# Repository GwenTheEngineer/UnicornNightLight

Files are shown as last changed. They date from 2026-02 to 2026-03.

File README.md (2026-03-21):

# Unicorn Night Light

This is the first time I've documented and open-sourced a weekend project!

If this project is helpful, you can support future side quests ☕
https://buymeacoffee.com/GwenTheEngineer

[YouTube playlist](https://www.youtube.com/playlist?list=PLPH9-bBXNwrTy-LLMLCjv-cOZETsQUVa1) for this project.

## Idea
This project brings to life the following vision for a table-top night light.

* Unicorn shaped shell
* Star shaped holes (through which the light will project)
* Moves up and down .... but *not* in circles (to avoid the user getting dizzy)
* Preferably rainbow colored

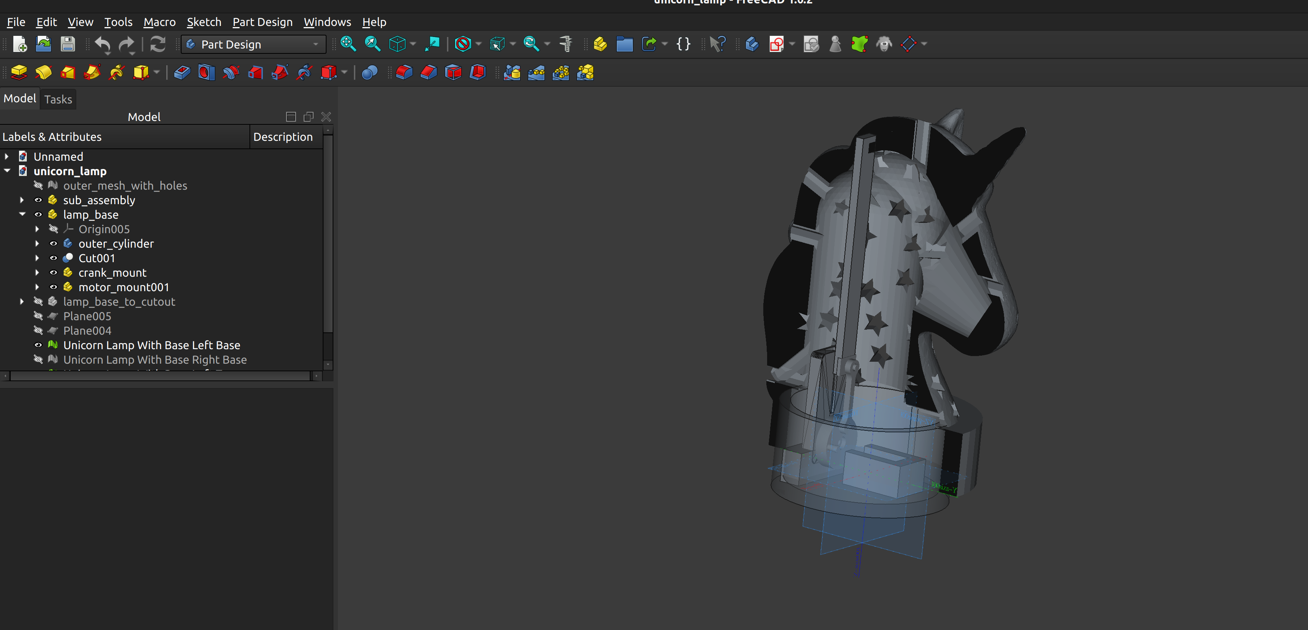
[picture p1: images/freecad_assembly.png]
Unicorn Nightlght Assembly


## Conceptual Design

A back of the envelope sketch of the vision! Doesn't need to be perfect, just needs to communicate what we want to accomplish. 

## Research

### Printable Parts

First, I needed a mechanism that could convert angular movement to linear movement...but I didn't know the right word for it. So I googled. Turns out, the word is "crank". Then, because my CAD skills are pretty elementary, I searched by go-to resource (printables.com) for a model that would work as a starting point -- with some resizing and adjusting to accommodate the motor shaft.

### Electrical and Mechanical

My hardware-adjacent and hobby background helped here. I hopped on amazon to find a low speed motor, appropriate transformers and adapters, and some LEDs and heat sinks. The complete BOM is listed below (NOTE! s.t. change; will remove this note when the project works).

Key considerations if you're shopping for your own parts:
* Motor size and speed -- I wanted something small (to fit inside) and low speed, but high enough torque to deal with the weight of the head and friction of the crank.
* Power supply -- wall sockets are AC; almost all hobby parts need DC
* Match voltages -- motor calls for 3.3-5V; you may need to step down your voltage after you transform AC-->DC
* Heat -- heat sinks help keep the temperature down.
* Materials! (see error log) Turns out after a few minutes, the PLA printing material deforms enough so the the outer shell stops going up and down (which is the whole point). Swapped to RC car pinion gears instead of directly driving the crank from the motor. 

## Detailed Mechanical Design

### CAD

I'm an engineer, but not *this* kind of engineer (professionally, at least). I did play with meshes in grad school, and CAD for mechanical design as an undergrad, but I was rusty when I started this project.

### Tl;dr

* I used FreeCAD (https://www.freecad.org/), Blender  (https://www.blender.org/), and Tinkercad (https://www.tinkercad.com/)
* Blender for mesh coarsening (in order to import the unicorn head mesh into FreeCAD and Tinkercad)
* FreeCAD to create the primitives to hollow out the head
* Tinkercad for booleam operations (i.e., actually subtracting the hole from the shell; adding the star holes)
* FreeCAD to ensure mechanical fit of the crank parts and motor mount and extending the slider / attaching it to the outer unicorn head shell
* Tinkercad for final adjustments (adding a collar, subtracting the base, making the hole to attach the slider column to the unicorn shell)
* FreeCAD for tweaking hole sizes to fit the motor and adding a through hole for the power cable to the base.
* FreeCAD to extend the slider mount (by slicing and tiling the original) and add a second bearing to the extended slider column
* ~~Blender to bisect the unicorn head in order to fit it on my printer (a Prusa Mini) -- See notes; this was a fun exercise but did not turn out to be necessary~~

### Play by Play
#### Outer Shell
Like most projects, this turned out to be more complicated than I had originally envisioned. (Engineers are notoriously bad at estimating).

Professional CAD tools are expensive. My favorite tool for small projects because it's very easy to use is tinkercad (online-only tool from the makers of AutoCad), free for individual and educational purposes.

For this project, that wouldn't work because the unicorn mesh was too big. After some research, I selected FreeCAD. Don't forget to leave a donation!

The big mesh was still causing problems, and free cads discretization didn't "just work". It's been a hot second, but I have used Blender for generating graphics for academic projects in the past. So I installed Blender, imported the mesh, used Blender's decimation tools, then went back to FreeCAD.  

After refining the mesh, I imported it back into FreeCad, then used primitives (cylinders, spheres, cones) to hollow out the unicorn head.

Next pain point was converting the unicorn shell to a solid in order to subtract the hole. FreeCAD recommends a max of 20k triangles; it was still too big (I tried to wait to let the CPU do it's thing, but it was hung)

But! Now I could import both parts into tinkercad and cut the hole out that way! So I decided to make the full shell in tinkercad, and return to FreeCAD (which I do want to learn) for the moving parts.

Back to FreeCAD to adapt the crank parts!

I imported the crank parts separately and "assembled" them for sense of scale. The general plan was to fit them in then scale the unicorn if necessary to make more room. I decided I would add mounts for the PCBs and LEDs later once all of the moving parts were put together. (Or, just wedge them in for now and come back to that in the next rev).

I needed one last import into free cad to cut the base out of the unicorn when all measurements were finalized. I scaled the unicorn up slightly from the original, and added a "cup" at the bottom to wedge PCBs and wires into.

One more round trop from FreeCAD to Tinkercad to get the hole at the bottom correctly sized; I had to add a collar (I just did this in Tinkercad) to maintain the wall thickness.

Finally! I split the unicorn by planes (in FreeCAD) and went to plate it ... forgetting that I needed to have the edges filled (with the cutout, it's just 2 nested meshes.) CAD programs generally aren't great at mesh editing. Back to Blender.

This article was useful: https://blender.stackexchange.com/questions/338870/bisect-separate-move. Don't forget to select "Fill" when you're bisecting. 

I rearranged the resulting objects into 2 collections, and duplicated the new faces in each collection, then, I went back to object mode and joined all objects, and then back to merge the meshes by distance (this removed a few hundred vertices each time).

#### Finalizing the Crank

~~First, I cleaned up the original mesh by removing the tab meant to demonstrate the part manually. I did this in Blender, but probably could have converted to a solid in FreeCAD and made the updates there, since it's a pretty simple mesh.~~  (see error log; this was actually not meant for fingers, it was a necessary part)

After the motors came in, I measured the shaft diameter at 3mm, with a flat face about 2mm wide. I then proceeded to accidentally use 3mm as the radius when updating the hole in the crank. F. This had to be redone. ~~On the bright side I only had to fix the hole in the crank, because the default size for the part attached to the base was just about right (I'll file it down after it prints if it's an issue).~~

#### Finalizing the Base
We need to punch a hole for the power cord to go through!

###### Rework #1 - crank orientation and hols sizing
I went ahead and made all of the holes bigger (1.8-2mm radius; see parts for details) for a better fit and reduce the amount of sanding I'd need to do for the mechanism to be smooth.

The slider mount needed to be flipped (:facepalm:). In the original orientation, the motor shaft would have interfered with the rod of the crank. To accomplish this in FreeCAD without changing the position of the column relative to the base, I placed the slider+column part directly over the crank to fit part, then rotated and adjusted the parts until the columns were overlapping the the crank was flipped 180 degrees relative to the motor mount.

I also extended the column by about 2cm to correct for the error of measuring the original height from slider's top position instead of the bottom. Oops.

###### Rework #2 - extend the slider mount; add 2nd bearing
I extended the slider mount and add a second bearing to limit the moment induced by the unicorn head on the slider. When mounted, it was pulling the crank off of the motor shaft.

###### Rework #3 - swap drive train; update parts accordingly
This was a pretty extensive rework. It involved updating the model to accommodate
(1) a gear attached to the end of the motor shaft, 
(2) a through-hole for the 2nd gear which will actually drive the crank, and
(3) adaptation of the crank parts to attach to a 3rd gear to drive the slider.

I did a save-as before starting this (new file is `unicorm_lamp_gears.FCStd`)

## Resources

### 3D Models

Crank Mechanism: https://www.printables.com/model/632627-crank-mechanism 

Unicorn Head: https://www.printables.com/model/1155402-unicorn-head

3D Printer: https://www.prusa3d.com/product/original-prusa-mini-semi-assembled-3d-printer-enclosure-bundle-5/

You don't actually need your own 3D printer; there is a growing number of public libraries, schools, and maker spaces where you can find them.

### BOM

These are affiliate links to fund a small percentage of reaching my Balmer peak (3-5% commission, depending on the part). Yay late stage capitalism. Let me know if you have a better resource and want to give Bezos less if your money.

As of this writing I have not tested any of these, so the list may change. I'll remove this comment when this is final.

#### Electrical Components
* Low speed (tiny) motors: https://amzn.to/4qAXlMr
* LEDs: https://amzn.to/469XHT5
* Heat sinks: https://amzn.to/3ZFIS6Y
* DC Low Voltage Speed Controller: https://amzn.to/4qSYteF
* Universal AC Adapter: https://amzn.to/4azepfL

#### Drive Train
* Steel RC Car Gears (38T and 42T used): https://amzn.to/47XY2c8
* Brass RC Car Gears (36T used): https://amzn.to/4bpC8AX
* 3mm Diameter Dowel: https://amzn.to/4bpC8AX 

(Same size in brass gears should be fine.)

#### Useful Tools
* Nail kit (useful for cleaning up support material from meshes): https://amzn.to/4s3IJGH
* Small electronics shopping cart (solder, wires, etc.). This is similar to what I've accumulated: https://amzn.to/4tOZ03W

## License

Unless otherwise noted, the documentation, images, and written content in this project are licensed under the Creative Commons Attribution-NonCommercial-ShareAlike 4.0 International License.

You are free to share and adapt this material for any non-commercial purpose, as long as you give appropriate credit.

## Disclaimer

This project is provided for educational and informational purposes only.

You assume all responsibility and risk for using the information, code, hardware designs, and instructions provided here. I make no guarantees regarding safety, reliability, or suitability for any purpose.

By attempting this project, you agree that I am not liable for any injury, damage, loss, or other issues that may occur as a result of building or using this project.

*Always follow proper safety practices when working with electronics, tools, and power sources.*

## Error Log (Learning!)

### Printing Orientation

Initially I thought of printing the unicorn on its side for 2 reasons (1) to fit on the build plate and (2) to minimize support material not directly on the build plate; i.e. to avoid digging support material out of the unicorns nose. The unicorn's horn did not stick to the plate -- it lifted. Also, the filament I'm using is rainbow -- so printing each side separately would cause a weird discontinuity in the rainbow. Since I had to bisect the head twice (X and Z planes) to fit anyways, I might as well try printing from the bottom up.... back to Blender. I also adjusted the settings (angle) when computing necessary support material.

*I reduced the angle to 45 degrees and swapped to organic support (which is often easier to remove).*

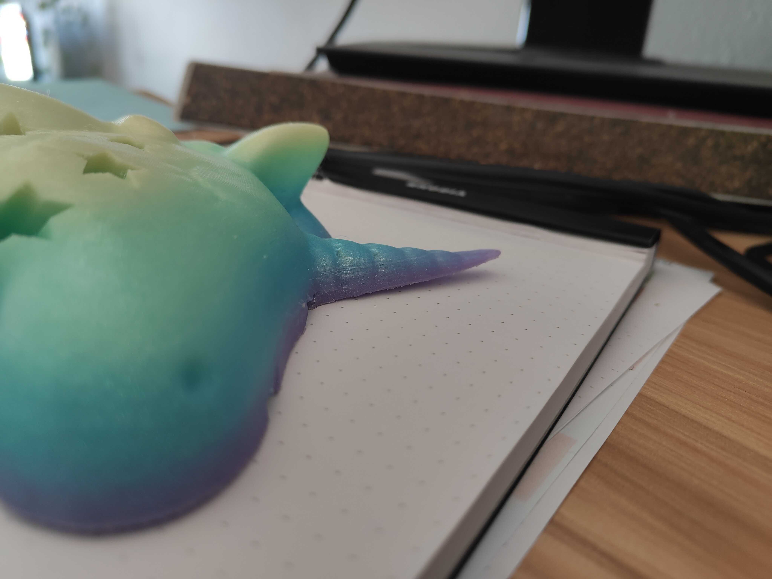
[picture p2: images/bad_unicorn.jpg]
Unicorn Nightlght Assembly


### Blender Hanging Splitting Loose Parts

The number of time Blender hung after bisect --> split faces by edges --> separate loose parts was frustrating. For some reason, it was trying to split ALL of the triangles into separate parts. This seemed to happen consistently when I bisected in the Z-plane (top from bottom) first.

In the end, I realized I could just print the whole unicorn, so went with this option (better for rainbow filament continuity).

The best work-around I found was duplicating the mesh and bisecting each instance; keeping the inner on one and outer on the other.

### Holes, Orientations, Mounts, and Tolerances

The motor shaft did not fit through the center holes on the crank. I went back to FreeCAD and made them 1.5mm wider. The hole on the crank mount was also too low by 1-2mm, so I moved that whole part up. I also upped the size of the holes in the crank's rod to reduce the amount of sanding I would need to do on the other crank parts to get a smooth motion.

In further facepalm-inducing mistakes, I computed the column height (the column connects the slider to the unicorn head) from the *top* position of the slider -- which meant it was several centimeters to short. This part also had to be redone.

Finally, the crank was actually backwards. The motor shaft and rod would interfere with each other. Oops.

Unicorn Nightlght Assembly

### Full Assembly Wobbles

Hindsight is always 20/20. With the base assembled, I was initially please with the fit of the motor shaft into the crank. The mechanism moved up and down about as smoothly as one would expect from PLA parts. HOWEVER, when the shell was placed on top, there was enough of a moment to pull the crank off of the shaft, even with the addition of glue.

This caused another re-work of the base (slider mount) and slider. I increased the width of the slider column so it sits closer to the mount, and added a second bearing to the slider. Then, I extended the height of the slider mount to accommodate the second bearing.

### PLA Material Failure
This required a pretty extensive rework. With everything wired up and the unicorn going slowly up and down (per the spec), the square hold at the center of the crank (printed with PLA) warped enough that the motors shaft started slipping. In retrospect, given the weight of the head and the nature of PLA, this was, in fact, foreseeable.

I needed a harder material; either metal or a different plastic (and preferably not too expensive). The solution: RC car parts and metal dowels! Then, updated the crank mount to accommodate 
(1) a gear attached to the end of the motor shaft, 
(2) a through-hole for the 2nd gear which will actually drive the crank, and
(3) adaptation of the crank parts to attach to a 3rd gear
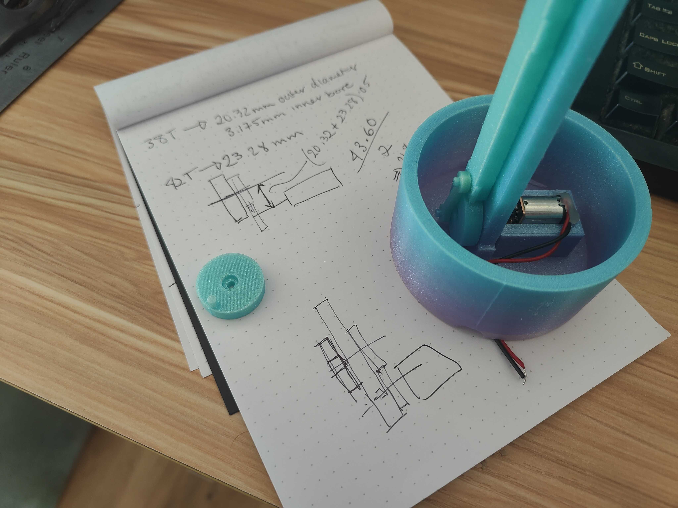
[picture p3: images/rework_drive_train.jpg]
Rework Drive Train


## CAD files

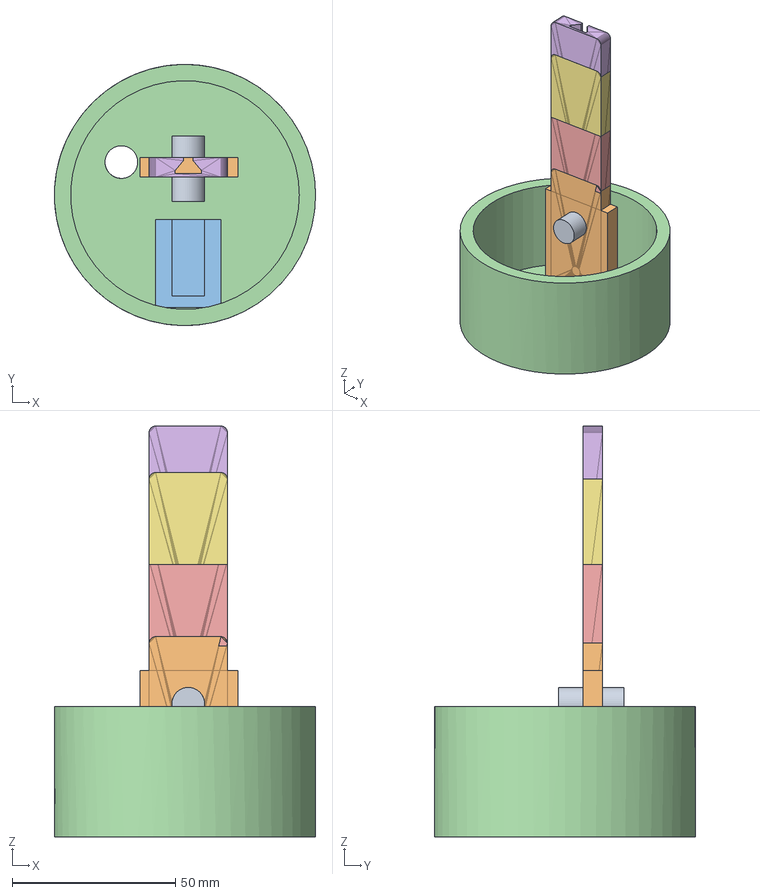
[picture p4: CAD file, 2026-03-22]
freecad/unicorn_lamp_gears.FCStd
80.0 x 80.0 x 125.9 mm
motor_mount_cutout001
base_cup_with_hole
Slice003.1
Slice003.004
Slice003.002

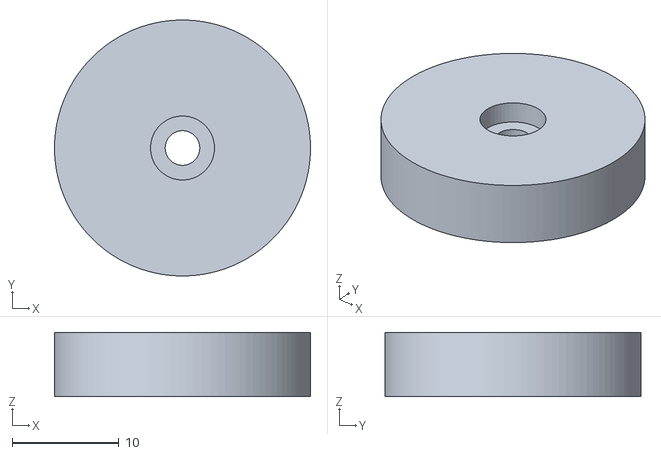
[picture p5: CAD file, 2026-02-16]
meshes/original/crank_clearance_fit_clean.stl
24.0 x 24.0 x 6.00

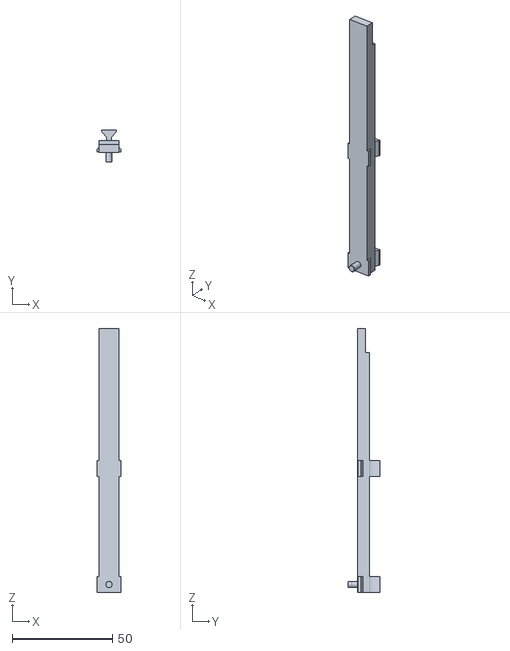
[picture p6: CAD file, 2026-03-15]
meshes/printed/direct_drive/unicorn_lamp-slider_double_support.stl
12.0 x 16.2 x 132.0

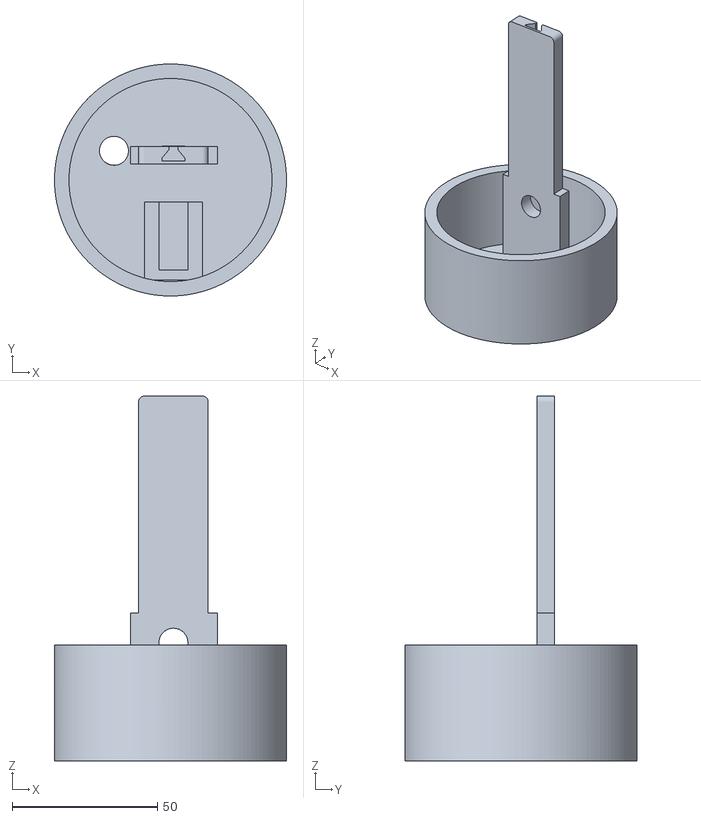
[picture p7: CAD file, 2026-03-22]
meshes/printed/gear_drive/unicorn_lamp_gears-lamp_base.stl
80.0 x 80.0 x 125.8

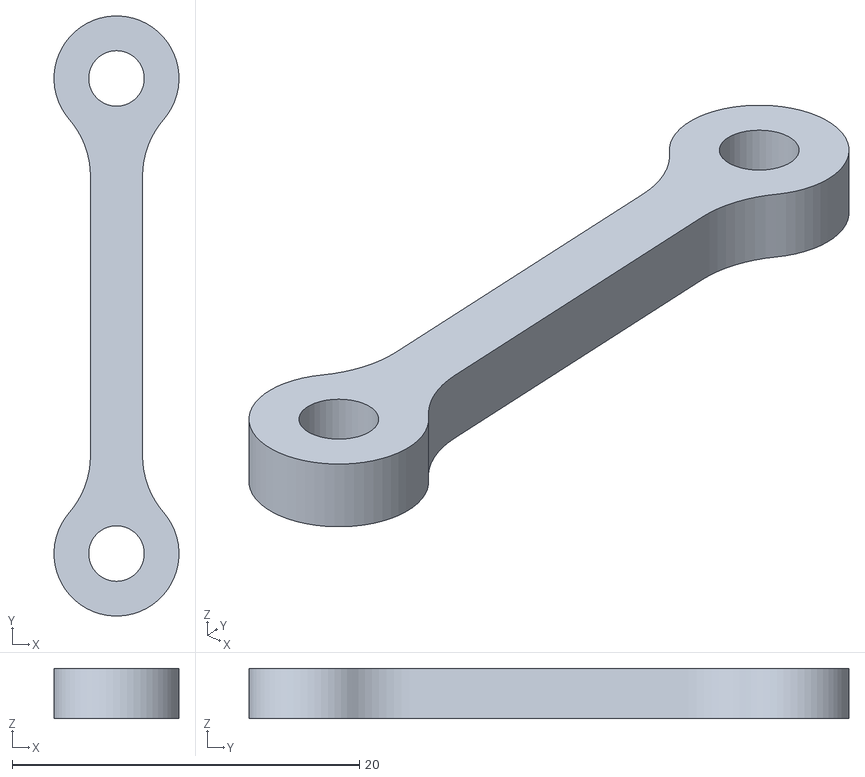
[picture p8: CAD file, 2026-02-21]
meshes/printed/unicorn_lamp-rod_bigger_holes.stl
7.19 x 34.5 x 2.90

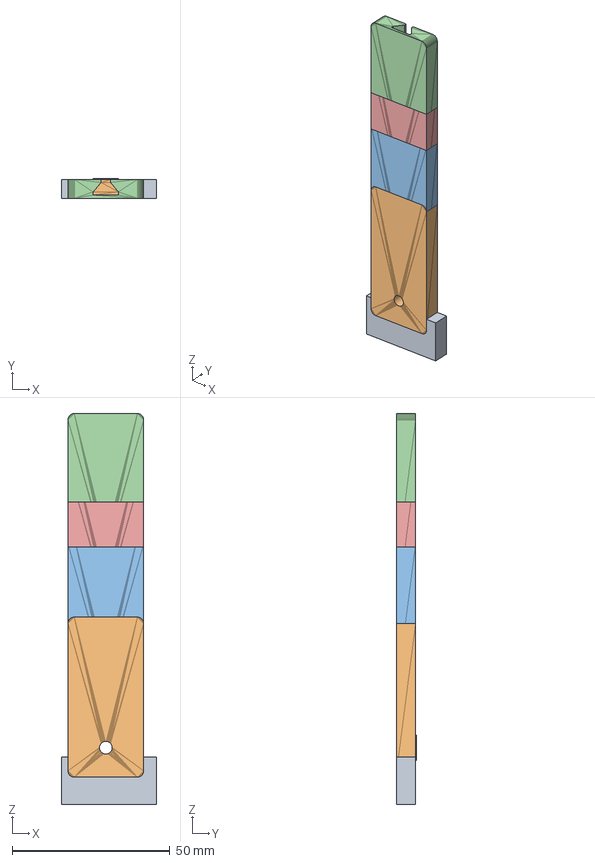
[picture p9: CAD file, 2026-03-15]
freecad/unicorn_lamp.FCStd
30.0 x 6.20 x 123.9 mm
crank_to_base_mount
crank_base_larger_hole
Slice003.1
Slice003.004
Slice003.002

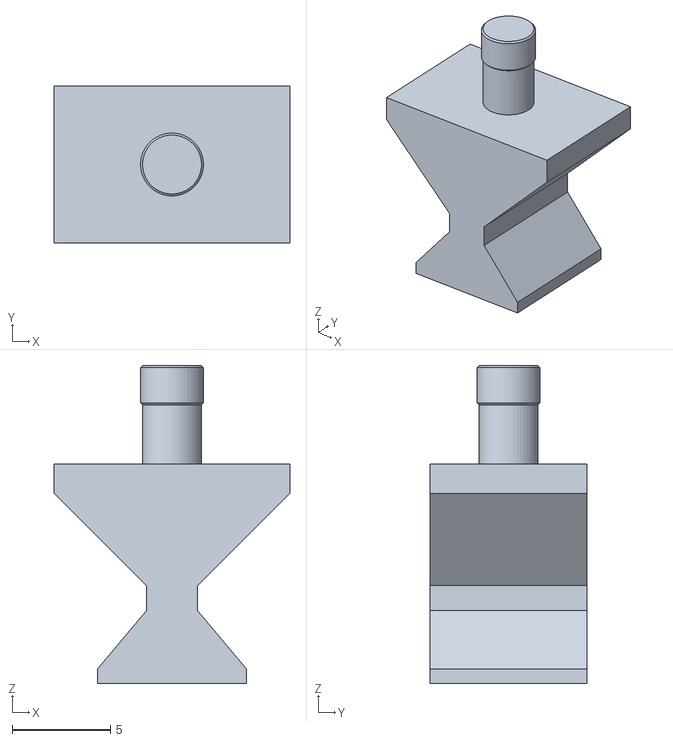
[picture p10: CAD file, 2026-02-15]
meshes/original/slider_clearence_fit.stl
12.0 x 8.00 x 16.2

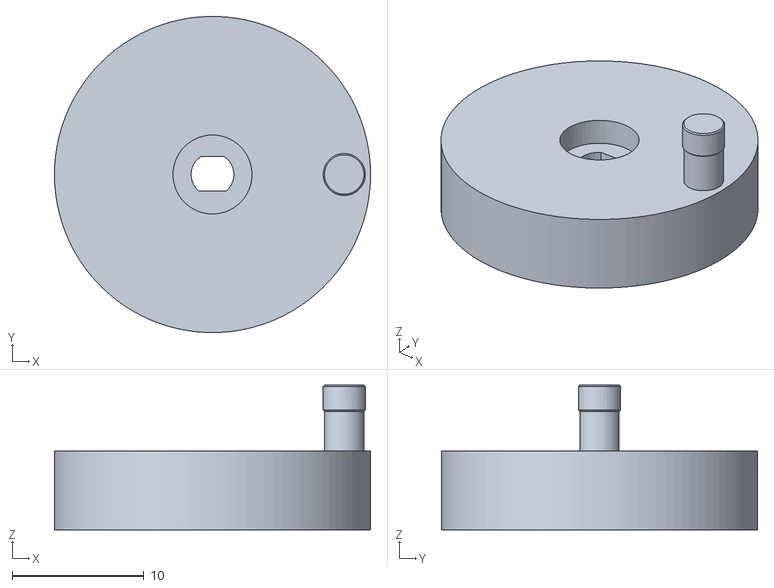
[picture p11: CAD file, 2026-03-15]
meshes/printed/direct_drive/unicorn_lamp-crank_with_flat_hole.stl
24.0 x 24.0 x 11.0

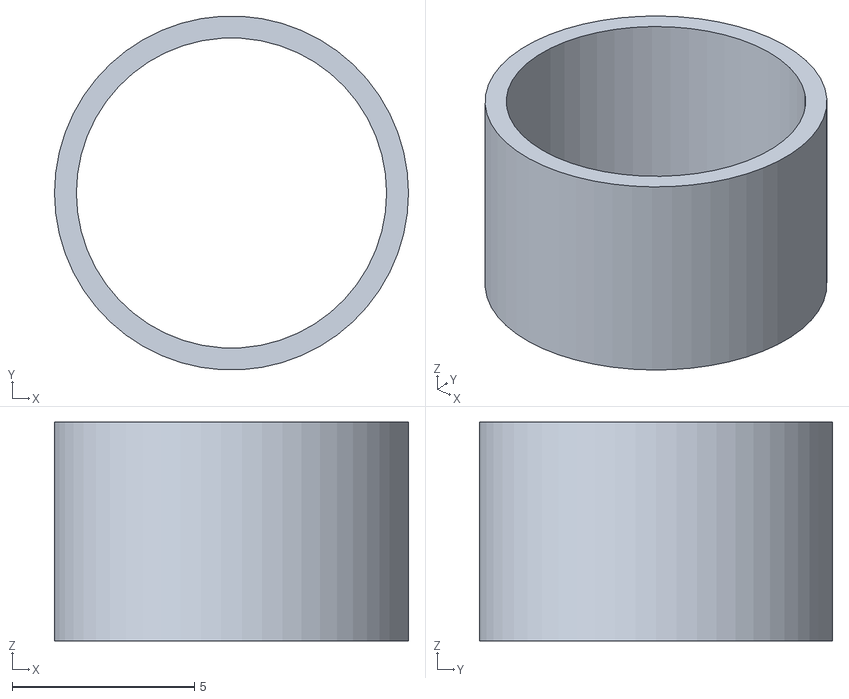
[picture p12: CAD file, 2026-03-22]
meshes/printed/gear_drive/unicorn_lamp_gears-resize_hole.stl
9.70 x 9.68 x 6.00

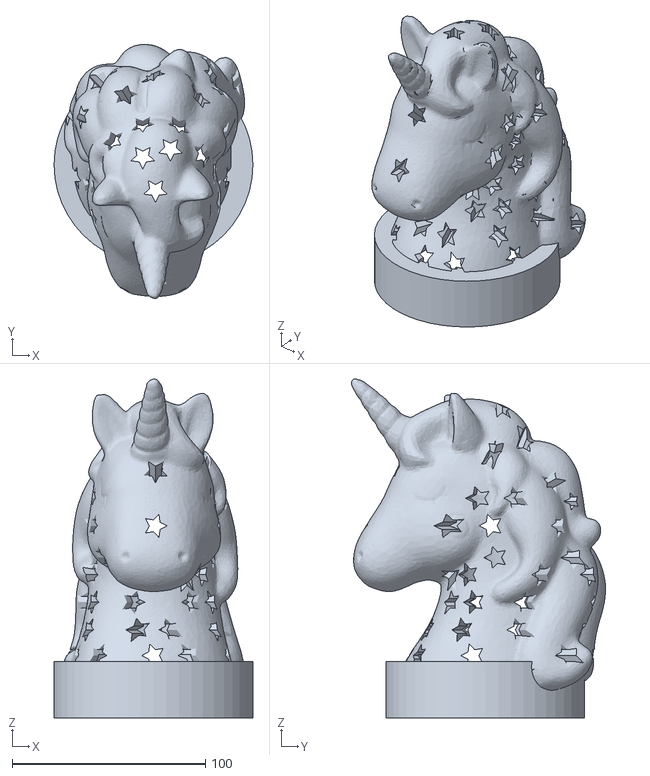
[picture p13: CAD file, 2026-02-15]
meshes/printed/unicorn_lamp_outer_with_base.stl
103.0 x 131.5 x 175.6

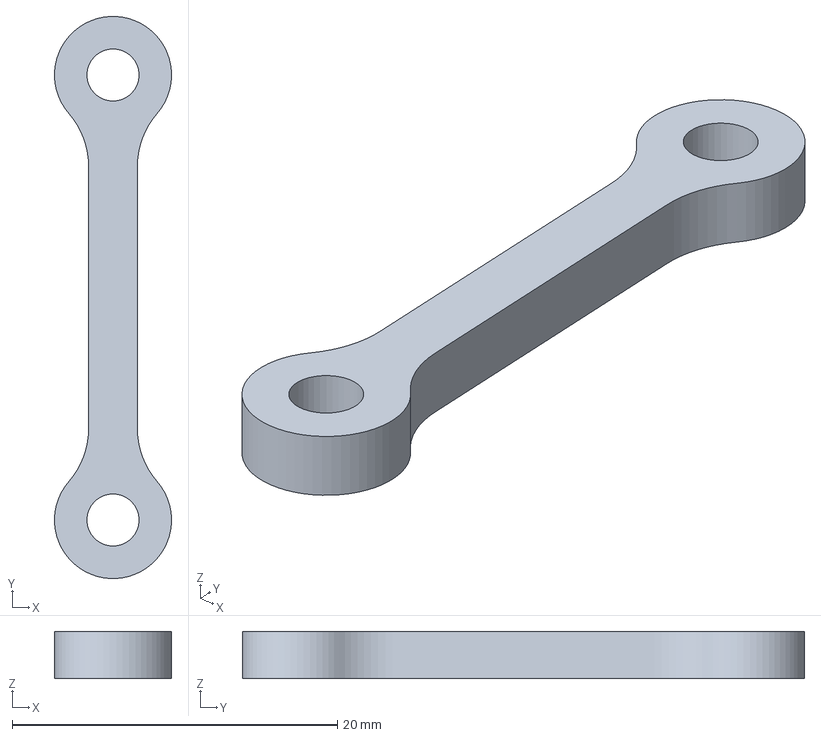
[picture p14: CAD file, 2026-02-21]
freecad/crank_for_mechamical_fit.FCStd
7.19 x 34.5 x 2.90 mm

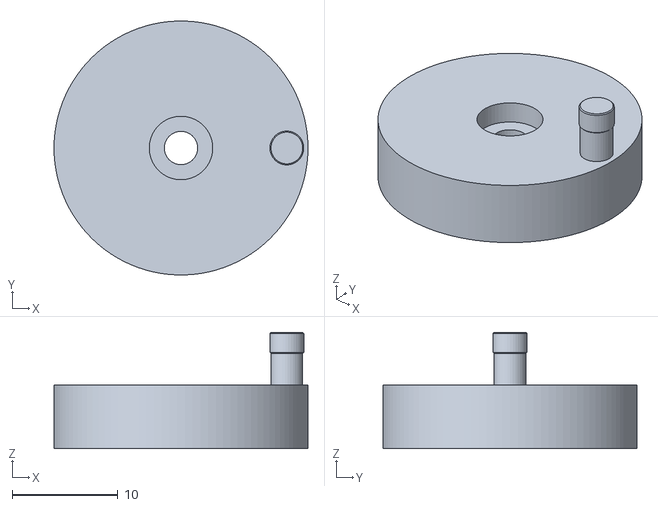
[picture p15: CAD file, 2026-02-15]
meshes/original/crank.stl
24.0 x 24.0 x 11.0

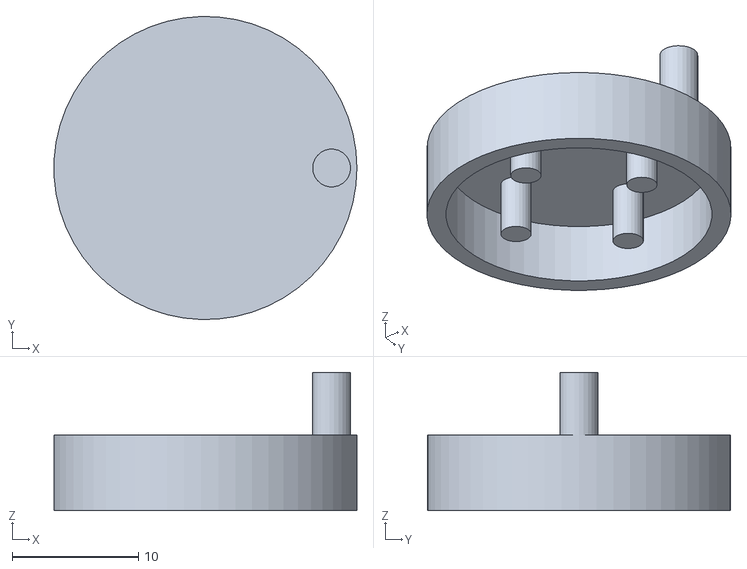
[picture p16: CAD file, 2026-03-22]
meshes/printed/gear_drive/unicorn_lamp_gears-crank_for_gear.stl
24.0 x 24.0 x 11.0

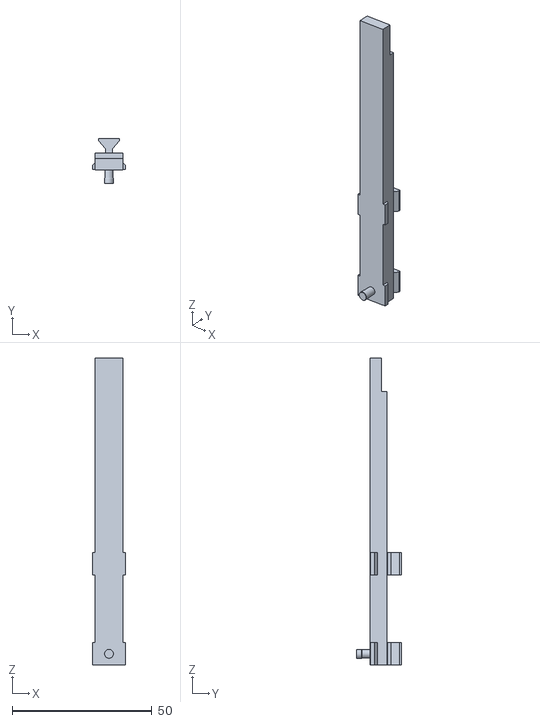
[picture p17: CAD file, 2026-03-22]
meshes/printed/gear_drive/unicorn_lamp_gears-slider_double_support.stl
12.0 x 16.2 x 110.0

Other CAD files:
meshes/printed/direct_drive/unicorn_lamp-lamp_base.stl
meshes/original/crank_clearence_fit.stl
meshes/printed/gear_drive/unicorn_lamp_gears-rod_bigger_holes.stl
blender/crank_cleanup.blend
blender/unicorn_bisected.blend

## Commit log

2026-02-15 WIP - meshes, README, blender, etc.
    [crank.stl, crank_clearence_fit.stl, crank_for_mechamical_fit.FCStd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]
2026-02-15 license and disclaimer
    [unicorn_lamp.FCStd]
2026-02-16 clean up mesh organization; update README for crank cleanup; commit plated parts
    [crank_and_rod.3mf, crank_cleanup.blend, crank_clearance_fit_clean.stl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]
2026-02-16 add initial BOM
    [unicorn_lamp-lamp_base.3mf, unicorn_lamp-lamp_base.stl, unicorn_lamp.FCStd]
2026-02-16 add youtube link
    [unicorn_lamp.FCStd]
2026-02-21 updated cad; updated printed meshes
    [crank_for_mechamical_fit.FCStd, slider.stl, unicorn_lamp-crank_slider_with_column_fused.3mf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]
2026-02-21 README and parts updates for more mistakes
    [crank_and_rod.3mf, unicorn_lamp-crank_slider_with_column_fused.stl, unicorn_lamp-lamp_base.3mf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]
2026-02-21 Flip crank mount; re-plate parts; update error log with image
    [unicorn_lamp-crank_slider_with_column_fused.3mf, unicorn_lamp-crank_with_flat_holecrank_with_flat_hole_cut.stl, unicorn_lamp-lamp_base.3mf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]
2026-02-21 add electronics cart to README
    [unicorn_lamp.FCStd]
2026-02-22 commit tweaked meshes
    [crank_and_rod.3mf, unicorn_lamp-crank_slider_with_column_fused.3mf, unicorn_lamp-crank_with_flat_holecrank_double_flat_hole.stl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]
2026-02-22 rework base and slider for double support; clean up freecad project
    [unicorn_lamp-lamp_base.stl, unicorn_lamp-slider_double_supportslider_double_support_final.stl, unicorn_lamp.FCStd]
2026-03-15 3rd rework notes and intermediate cad
    [unicorn_lamp-crank_with_flat_hole.stl, unicorn_lamp-slider_double_support.stl, unicorn_lamp.FCStd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]
2026-03-21 reorganize meshes
    [crank.stl, crank_clearance_fit_clean.stl, crank_clearence_fit.stl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]
2026-03-21 update deadme with RC part BOM
2026-03-22 fix placement of pegs in crank; part to adjust hole size
    [unicorn_lamp_gears-crank_for_gear.stl, unicorn_lamp_gears-resize_hole.stl, unicorn_lamp_gears-rod_bigger_holes.stl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]
2026-03-22 bearking for hole; tweak final position after testing
    [unicorn_lamp_gears-lamp_base.stl, unicorn_lamp_gears-resize_hole.stl, unicorn_lamp_gears.FCStd]
